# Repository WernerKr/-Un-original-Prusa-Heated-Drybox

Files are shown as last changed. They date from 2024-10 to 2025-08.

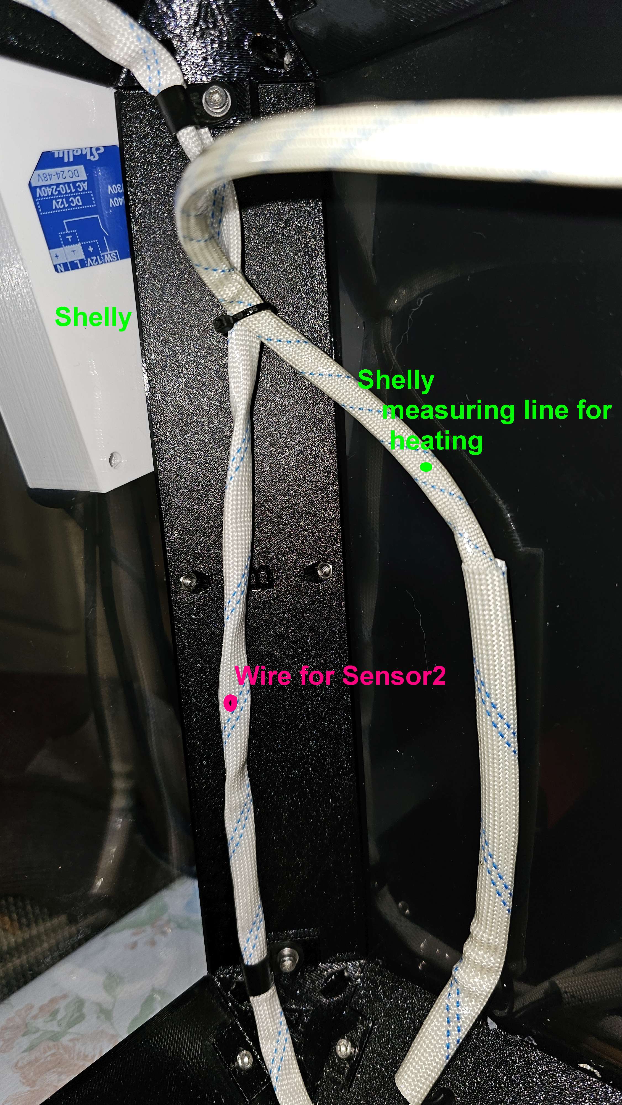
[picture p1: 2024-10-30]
drybox/Wire Sensor2.jpg

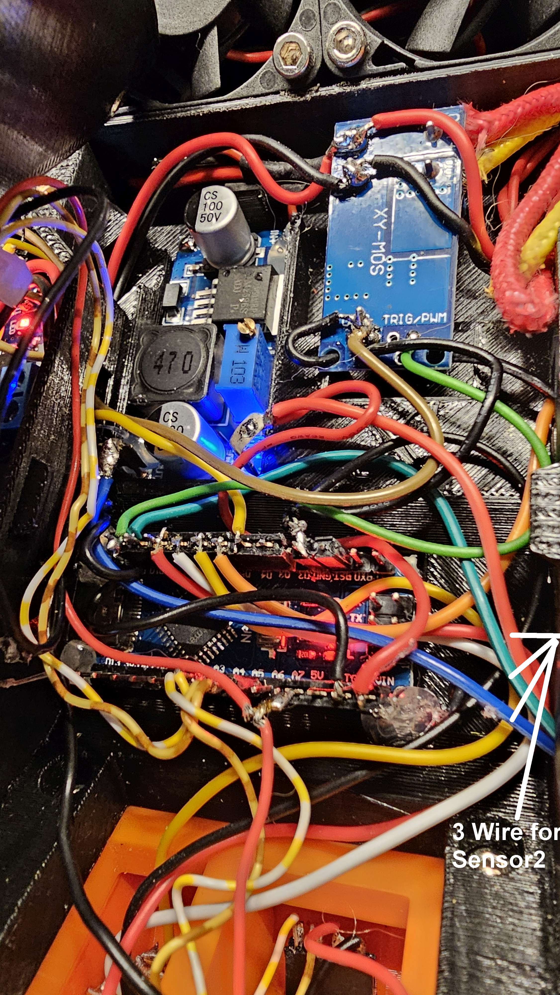
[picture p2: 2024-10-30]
drybox/Wire3 Sensor2.jpg

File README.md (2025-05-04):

## -Un-original-Prusa-Heated-Drybox Code for Ardunio Nano ESP32-S3 Home Assistant

Required processor Arduino Nano ESP32-S3, is pin compatible and has the same dimensions as the Arduino Nano 
with the exception that the 5V pin only supplies a voltage when USB is connected. 
Therefore, no more 5V is taken from this pin, only from buck converter (or Vin Pin, whereas this Pin is always connected to buck converter).
- Invalid values (85°C or -127°C and now too >150°C) are displayed as 0.0 °C/F but are not transmitted to Home Assistant.

#### The esp32 3.1.1 board library is needed!. The newer esp32 3.2.0 board library is causing errors. 

IDE_Arduino_Nano_ESP32
Arduino Nano ESP32 Drybox

### Update 2025-02-07
- Fan run-on now depends on the temperature reached
- If #define BlankScreen and #define BlankScreenAutoOff are active and AutoHum is also active, the screen saver is activated after the heating and fan are off (Pixel).
- To get the display back, press the "Down Button". The display is then activated for 1 minute (countdown 30) and you can then also reduce the target temperature here.
- If the humidity rises again (heating on again), the display is immediately activated again.

##### Graphic AutoHum 27%
AutoHum_27

#### All user settings are now stored in the file arduino_settings.h
- The former "down" Button (was Second Temp/Hum on/off) is now for ScreenSaver
- The former PIN D4 for Led is now D3. 
- The DS18B20 data works only with PIN D4.
- But to use it, the GPIO pin = 7 for D4 must be set.
- To connect the DS18B20 temperature sensors (3 are supported in the program code) a 4.7 KOhm resistor must be used between pin D4 and Vin (=5V). All data lines of the DS18B20 are connected to pin D4 at the same time.
- Since the Arduino Nano Esp32 has a higher internal temperature, the DHT20 heats up more and the temperature value is therefore distorted when the heating is off.
- Therefore, it makes sense to move/mount the DHT20 sensor outside the Z-bracket, perhaps above the Z-bracket near the fan
drybox2_dht20

#### All user settings are now stored in the file arduino_settings.h
- #define debug -> to see the Temp/Hum Data and DS18B20 addresses in the Serial Monitor
- #define showFraction -> all values with decimal values otherwise only integer values
- #define controlLed -> if an LED strip needs to be controlled ("up" Button) in non-heating mode
- #define ControllLedAutooff -> Led on and Temperature >=60°C/140°F (= max. operating temperature LED strip) the led is switched off
- #define SecondTemp -> if a second temp/hum is available - not tested without this - so should now always set
- #define BlankScreen -> on/off ScreenSaver with "down" Button in non-heating mode
- #define UsePixel -> ScreenSaver is "running Pixel" otherwise blank Screen
- #define BlankScreenAutoOff -> if heating is off sreensaver active after 10 minutes - need also #define UsePixel
- #define WATCHDOG -> the program is monitored with WatchDog
- #define HomeAssistant	-> send data to Home Assistant
-         security, lan and Name settings for Home Assistant
- #define DS18B20xx -> also support and show DS18B20 temperature sensors
- #define DS18B20HA -> DS18B20 data also send to Home Assinstant, should only be set after the sensor address assignment has been made
- #define DallasAdrSet -> are the DS18B20 temp sensors adresses above correct? Should be set so that the sensor order always remains the same
- #define DallasSensor1 -> first DS18B20 temp sensors available
- #define DallasSensor2 -> second DS18B20 temp sensors available
- #define DallasSensor3 -> third DS18B20 temp sensors available
- all other settings (targetTemp, targetHum ...)

#### ScreenSaver Mode:
The reason why this function was introduced is that the used OLED display produces "ghost characters" when used for a long time and eventually becomes illegible. This extends its lifespan.
Usage: Switching on/off is only possible in non-heating mode using the "Down" button. As soon as heating mode is started, the ScreenSaver is switched off, with the exception: with AutoHum and the heating and fan are off, the previously set ScreenSaver mode is activated again. There are two types of ScreenSaver: The default is that a pixel moves across the screen every 2 (AutoHum heating mode) or 10 (off mode) seconds. The alternative is (//#define UsePixel - i.e. not active) the screen is completely off.

#### DryBox 
With the appropriate settings, the program behaves just like the DryBox without ESP32, but can easily be expanded with the features of the ESP32 (Wifi, Home Assistant, DS18B20 Temp Sensor).

Home Assistant

### DryBox Home Assitant Graph

drybox_graph
Drybox2_graph

Drybox2_HA
drybox_ds18b20

# -Un-original-Prusa-Heated-Drybox Code for Ardunio (Nano) 
https://www.printables.com/de/model/883817-unoriginal-prusa-heated-drybox

Parts sold from Blurolls: processor ATmega328P (OldBootloader)

DryBox

Heater_off
Heater_on

Heater_offF
TargetTempF

AutoOff
AutoHum

With duct
Drybox_with_duct

## 2024-12-11: Updated files (Serial_20241211.zip)
 - In heating mode, the update and query interval has been reduced to 2 seconds
 - In addition, the temperature control difference was set to 0.1°C / 0.18°F and the humidity control difference (AutoHum) was set to 0.1% humidity.
 - This results in much faster control behavior (Inspired by Sunlu S4)
 - I am now using a modified duct, provided to me by @wbsp. Changes: 
 - the outlet area at the bottom is 5 mm larger and the outlet at the side is 12 mm higher. 
 - This allows for a much greater air flow. 
3D Druck_ 20241213_drybox1
3D Druck_ 20241213_drybox_hum

 ### Comparison with Sunlu S4
 Sunlu_S4_Sensoren2
 3D Druck_ 20241213_Sunlu_S4
 3D Druck_ 20241213_Sunlu_S4_1
 3D Druck_ 20241213_Sunlu_S4_0

## 2024-11-25: Updated files (Serial_20241125.zip)
 With AutoHum, the humidity difference has been reduced to 0.2% (previously 1.0% and 0.5%)
 If the AutoHum function is set below 25%, the TargetTemp is raised to 55°C/131°F, otherwise this humidity is not achieved. 
 The fan run-on time has been slightly reduced at temperatures above 55°C.

Diagram description:
 - At start-up TargetTemp = 50°C, AutoHum = 25%. The front door was still closed. 
 - At around 9:45 the front door was lifted slightly to allow air to circulate. 
 - At 10:30 the AutoHum value was reduced to 20%. Previously, the 25% was reached and regulated
 - After the AutoHum value was not reached at the TargetTemp of 50°C, the TargetTemp was raised to 55°C shortly before 11:00. 
 - With this setting the AutoHum value of 20% was then reached and regulated.
Drybox_Autohum1
Drybox_Autohum2

## 2024-10-15: Updated files (Serial_20241015.zip)
Possibility to switch off the LED strip automatically at 60°C/140°F, 
as the LED strips normally have a maximum operating temperature of 60°C. However, this requires a second Temp/Hum sensor.

## Comparison with/without duct, with/without additional fans
 #### Test environment: 
 - Target temperature 70°C, 
 - AutoOff after 240 minutes (4 hours), 
 - two empty filament rolls in position 2 and position 4.
 - Two front PTFE outlets always open for air exchange. 
 - Overtemperature shutdown of the heater at 90°C, measurement on the floor below the heater/duct
 - Measured with second temp/humidity sensor
 - Graphics from Home Assistant and data from Shelly Plus Add-on and 3 sensors DS18B20 - measuring range -55 °C to +125 °C
   
Drybox

- T1 = Heating temperature
- T2 = Temperature under heating/duct
- T3 = Temperature front right (near door)

### Temperature curve without duct and without additional fans
- The door was lifted slightly after about 1 hour for air exchange and closed again about 5 minutes before the end
- Temperature reached 64.2 °C and 
- temperature under heating 86.9 °C
Drybox_org_vx
### Temperature curve with duct and without additional fan
- The door was raised slightly after 5 minutes and was then raised the whole time for air exchange
- Temperature reached 55.8 °C and 
- temperature under duct 73.0 °C
Drybox_duct_vx
### Temperature curve with duct and with two additional fans below duct
- The door was lifted slightly after 5 minutes and was closed again 5 minutes before the end for air exchange
- Temperature reached 60.2 °C and 
- temperature under duct 71.5 °C
Drybox_fan_vx

## Older test:
#### New: two additional fans below the "duct" for much better air distribution
#### for Bracket Y, Beam A1, Beam A2, Beam A3, Beam A4, duct is now printed with Easy Nylon from Overture.
#### Heat resistance of PC blend is only 113°C/235°F, but over 120°C/248°F is achieved on Bracket Z and duct
#### Easy Nylon has a Heat resistance of 180°C/356°F

Fan 3and4
Fan 3and4_0
Fan 3and4_1
Additonanl_Fan0
Additional_Fan
### New measuring sensors: with Shelly Plus Add-on: DS18B20 - measuring range -55 °C to +125 °C

The second temp/humidity sensor now measures the temperature on the floor under the duct
```
The front door was slightly open
Temperature 2 : Temperature inside duct
Temperature 3 : Temperature Back below duct
Temperature 1 : Temperature front bottom right
Temperature 4 : Temperature rear bottom left
Temperature 5 : Temperature rear bottom right

3D : Temperature/Hum Front bottom right
3DL: Temperature/Hum Back bottom left
3DR: Temperature/Hum Back bottom right
```

### TargetTemp 70°C
TempGraph_TargetTemp70_1
TempGraph_TargetTemp70_2

### TargetTemp 50°C
TempGraph_TargetTemp50


## Heating test series:
```
Sensor Ecowitt WN34AD Temperature range -55..+125°C, Measuring cycle 77 seconds
```
Ecowitt WN34AD_0
```
Sensor DHT21  Temperature range -40..+80°C, here Measuring cycle 5 seonds
```
DHT21
```
Empty Box! With Duct from "morap"
WN34AD in the measuring hole of the duct
Second sensor DHT21 at the bottom of the box under the duct
```
Messung

```
DHT21 Duct: Previous measurement with DHT21 on the duct and temperature limitation at 123°C
```
```
All values are in °C - Time in minutes
Time 	WN34AD	Display	DHT21	DHT21 Duct
5	97.0	34.7	51.2	85
6	100.6	36.3	53.9	90
8	103.4	37.7	56.0	95
9	105.6	39.2	58.0
10	107.4	40.5	59.9
11	108.4	41.7	61.4	100
13	110.2	42.8	62.9	105
14	111.3	43.8	64.2	110
15	112.3	44.8	65.4
17	113.1	45.7	66.2	113	
18	113.8	46.6	67.4	115
19	114.5	47.3	68.2
21	115.1	48.0	69.0
22	115.6	48.7	69.5
23	116.1	49.3	70.2	119
24	116.6	49.9	70.8	
26	116.9	50.4	71.2	121
27	117.3	50.9	71.7	
28	117.6	51.4	72.0	122
29	118.0	51.8	72.4
31	118.2	52.2	72.7	123
32	118.5	52.5	73.0
33	118.8	52.8	73.4
35	119.0	53.1	73.7
36	119.3	53.4	73.9
38	119.6	53.9	74.4
40	120.0	54.2	74.7
41	120.1	54.4	74.9
42	120.2	54.6	75.0
43	120.3	54.8	75.2
45	120.5	55.0	75.4
46	120.7	55.1	75.5
47	120.8	55.3	75.6
49	121.0	55.4	75.8
```
Diagramm
```
3DL shows temperature curve at the rear left.
3D shows temperature curve at the front right
Depends greatly on the temperature at the back in the middle on the floor (directly under the duct last 75.8°C)!

```
### End of testing:
End
Ecowitt WN3434AD_1

## Code files for the heater 

### Main file = Serial.ino
Arduino IDE
ARDUINO_pin_en

Support a second temperature/humidity sensor (DHT21 or DHT22)
You need then additional the Arduino library "DHT-sensor-library"

SecondSensor1
SecondSensor2

Control the fan via a second mosfet
Can Control a led strip via a third mosfet
Heater AutoOff function.
Heater AutoHum function.
Overheating control (with second temperatur/humidity sensor) - not active if no second temp/hum semsor or disabled

Fan control: Vin+ to 24V+, Vin- to 24V-(Gnd), Out+ to Fan red, Out- to Fan black, Gnd to Buck-Convert Out- or Arduino GND
//Arduino pin where the control line for the Mosfet is connected
```
#define Fan 5
```
Led strip control: Vin+ to 24V+, Vin- to 24V-(Gnd), Out+ to Led red, Out- to Led black, Gnd to Buck-Convert Out- or Arduino GND
24V Led strip:
```
#define controlLed
#define Led 4
```
Led_strip_wire
Led_strip1
Led_strip_on

In the program, the second sensor is switched on with
```
#define SecondTemp
or deactivated with //#define SecondTemp
```
The sensor used is specified here
```
#define DHT_TYPE DHT21
//#define DHT_TYPE DHT22
```
The DHT21 is activated here
The data pin of this sensor is set to 9:
```
#define DHT_PIN 9
```
The other pins of this second sensor are to be connected to 5V and GND.

If the second sensor is activated but there is no second sensor,
0.0% and 0.0°C are displayed in the data line.

## Protection for the Wires
High temperature wire protection

If the heating is switched off, you can use the
#### "-" button (= bottom button) to switch on or off to the normal display (no display of the data from the second sensor).
-> Function not available if no second temp/hum sensor present

If the heating is switched off, you can use the
#### "+" button (= middle button) to toggle the LED strip off/on - default is on

In addition, you can use the program to display the data from the temperature/humidity sensors using
```
#define debug (default deactivated with "//#define debug")
```
via the IDE's serial monitor.
But this data are not updated if the AutoOff function is activ!

It is possible to correct the temperature and/or humidity values with a correction value.
```
float TemperatureCor = 0.0;
float HumidityCor = 0.0;
float Temperature2Cor = 0.0;
float Humidity2Cor = 0.0;
//The maximum adjustable temperature is limited to 70°C.
int MaxSet = 70;  
//The overheating temperature is set to 83°C - now measured under the duct!
int Max = 83;   
```
This is because the Arduino should only be operated up to a maximum temperature of 80°C.
If you want a higher temperature, you have to place the electronic components outside the housing! 

When the heating is switched on, you can activate the heating AutoOff mode by pressing the

 ### First and hold the "+" (middle button) and then "on/off" (above button) button.
You may have to try a few times until it works. The display shows then "AutoOff"

AutoOff

The default switch-off value is 360 minutes
```
int AutoOffTime = 360;
```
The maximum time for switching off is 2 days (2880 minutes)
```
int MaxAutoOffTime = 2880; // max 2 days, step 10 minutes
```
The minimum value is 10 minutes.

When the heating is switched on, you can activate the heating AutoHum mode by pressing the
 ### First and hold the "-" (below button) and then "on/off" (above button) button.
You may have to try a few times until it works.  The display shows then "AutoHum"

AutoHum

If the set Humidity value (10-65%), default 35% is reached the heater is switched off
the Fan delay starts and after the set time the fan is also switched off (only with extra Mosfet for fan!)
-> stand by. 
If the Humidity value increase the heater and fan is switched on again
and so on. 

The default Auto Hum value is 25 % - changed from 35% to 25%
```
int TargetHum = 25;
```
The maximum percent for standby = 65 %		// with so high value you can simple test the AutoHum function!
The minimum value is 10%			// This humidity level will probably not be reached with heating!



```
 On the picture you see a AutoHum value of 45% and the Heater is on (ON)
 The humidity value is 44.4% (AutoHum value reached) the Heater is off (on)
 The fan delay starts and the fan is also switched off in 230 seconds (need fan control).
 If the humidity rised to 46% the heater and fan is ON again. 
```
The settings of the AutoOff Minutes and AutoHum times is now automatical done after 30 seconds!
A dot will appear on the far right side if the change of the values of AutoOff or AutoHum is still active.
Otherwise, change the target temperature.

Settings

### Fan Control:
Function: when the heater is switched on, the fan always runs, even if the target temperature has been reached (heating element is switched off).
If the heating element is switched on in normal mode, this is now displayed with "ON".
If switched off, it is displayed with "on".
In AutoOff mode, a switched on heating element is displayed with "A" and a white background, 
if switched off, it is displayed with "A" and a black background.
When overtemperature is reached, "Hi" is displayed instead of "ON" and the heater is switched off until the temperature drops again.
In AutoOff mode instead of "A" then "H"

 Vertical Display hiTemp

When the heater is switched off (directly or via AutoOff), the fan continues to run for an adjustable time:
```
int FanDelay = 300;
```
Vertical Display

This run-on time is then counted down in the display after switching off.
The fan shutdown time now depends on the selected target temperature (60 - 900 seconds)

If you have installed a second temperature sensor, you can with 
```
bool overHeat = true;
```
monitor the temperature directly on the heating element and when the max temperature (°C)
```
int Max = 83;		// = 181 °F
```
is reached, the heating is also switched off (fan continues to run if second Mosfet is used)

Other settings:
```
#define showFraction
```
Now also in the State Line the Temperatur or Humidity are shown with fraction.
If you like the former showing (only Integer) uncomment //#define showFraction

AutoOff_HeaterOn_secondSensor_showFraction
AutoOff_HeaterOn_secondSensor_not_showFraction

If Duct is installed, the system is slower, so the change temperature is set to 0.2°C here, otherwise 0.5°C
```
bool withDuct = true;                     // Duct installed -> Tempdiff = 0.2°C otherwise 0.5°C
```

### But be careful: 
    all electronic components used (temp sensor, Arduino, etc.) are only designed for a maximum ambient temperature of 80°C (176°F).
    And you should also note: Maximum operating temperature of the fan is 70°C
    If using inside the (Un)original Prusa Heated Drybox a LED strip you should know:
    the maximum operating temperature of the LED strip is normally 60°C! 

#### Warning!
     If the fan control is not used, the fans must be permanently connected to the 24 V voltage.
     The display behaves as if the additional fan control were present, showing a countdown in seconds for the fan to shut down!

#### My recommendation for the filament to be used for "Bracket Y" and "condotto 5" is Nylon 
#### or an even higher temperature resistant filament.
#### In my experience, even PC blend or ASA is not suitable!

### Also important!
    When the heating is on, air exchange must be able to take place, 
    e.g. by lifting the front door or using the unused PTFE outlets, 
    otherwise humidity reduction cannot take place.



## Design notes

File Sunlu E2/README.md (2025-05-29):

## Sensors used:
- Sonoff SNZB-02D (Temperatures from -9.9°C to +60°C ) stopped at 59.9 °C - removed for Target 90°C and 110°C
- DHT20: Sunlu Temperatur außen unten (Temperatures from -40°C to +80°C ) but masures above +80°C
- DHT22: Sunlu Temperatur Innen (Temperatures from -40°C to +80°C ) but measures above +80°C 
- DS18B20: Sunlu Temp1, Temp2, Temp3 (Measures Temperatures from -55°C to +125°C ) stopped at 127.94 °C
- Camera: Flir One Pro
- Recording via Arduino Nano ESP32-S3
- Evaluation via Home Assistant
E2_Sensorsx_txt
Sunlu_E2_00

## Diagram at Target temperature 70°C, 90°C and 110°C
### Settings: Target temperature 70°C
#### Temperature and consumption diagram of the Sunlu E2 dryer 70°C
E2_70x

Sunlu_E2_70x
Sunlu_E2_70_1x
Sunlu_E2_70_2x
##### Inside
E2_inside_70x
##### Temperatures after switching off (70°C)
E2_after_Switch_offx
##### after 3 minutes (70°C)
E2_and_then_after_Switch_off_3minx

### Settings: Target temperature 90°C
#### Temperature and consumption diagram of the Sunlu E2 dryer 90°C
Sunlu_E2_90x
Sunlu_E2_90_1x
Sunlu_E2_90_2x

### Settings: Target temperature 110°C (max reached 106.13°C sucking the air) 
E2_Set_110x
#### Temperature and consumption diagram of the Sunlu E2 dryer 110°C
Sunlu_E2_110x
Sunlu_E2_110_1x
Sunlu_E2_110_2x
Sunlu_E2_110_3x
Sunlu_e2_110_end

### Inside
E2_Heating_110x
E2_Heating_110_2

### Outside (110°C)
E2_outside_frontx
E2_outside_front2x
E2_Outside_2x

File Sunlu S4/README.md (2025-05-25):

# Settings: Target temperature 70°C
#### Sensors used:
 - Sonoff SNZB-02D
 - DHT20: Sunlu Temperatur außen unten
 - DHT22: Sunlu Temp vor Ansaug
 - DS18B20: Sunlu Temp1, Temp2, Temp3
 - Camera: Flir One Pro
 - Recording via Arduino Nano ESP32-S3
 - Evaluation via Home Assistant

## Temperature and consumption diagram of the Sunlu S4 dryer
Sunlu S4

Sunlu_S4_00
Sunlu_S4_0
Sunlu_S4_1
Sunlu_S4_2

## Power consuption diagrams
Sunlu_S4_Leistung
Sunlu_S4_Leistung1
Sunlu_S4_Leistung2

## Temperature inside the dryer
2025-05-22 10 50 39x
2025-05-22 10 50 48x
2025-05-22 10 54 17x
2025-05-22 10 54 58x

## Outside Front
2025-05-22 10 53 21x
2025-05-22 10 49 52x
2025-05-22 10 51 31x
2025-05-22 10 42 24x

## older diagrams
3D Druck_ 20241213_Sunlu_S4_0
3D Druck_ 20241213_Sunlu_S4_1
3D Druck_ 20241213_Sunlu_S4

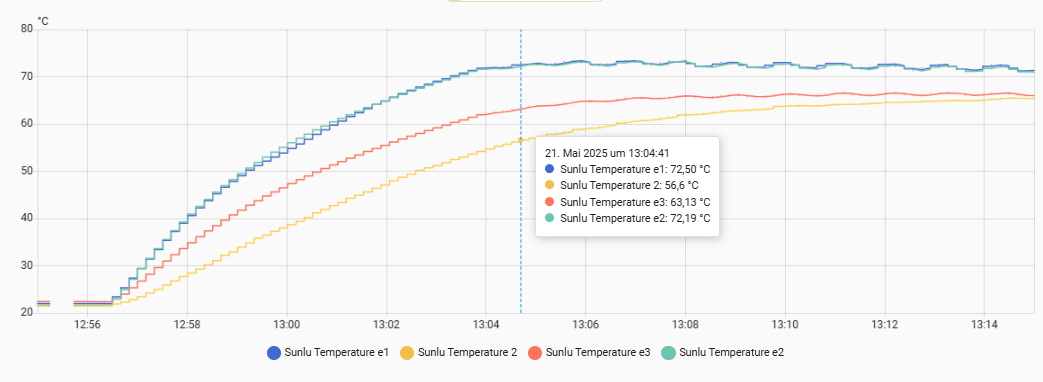
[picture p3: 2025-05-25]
Sunlu S4/Sunlu_S4_00.png

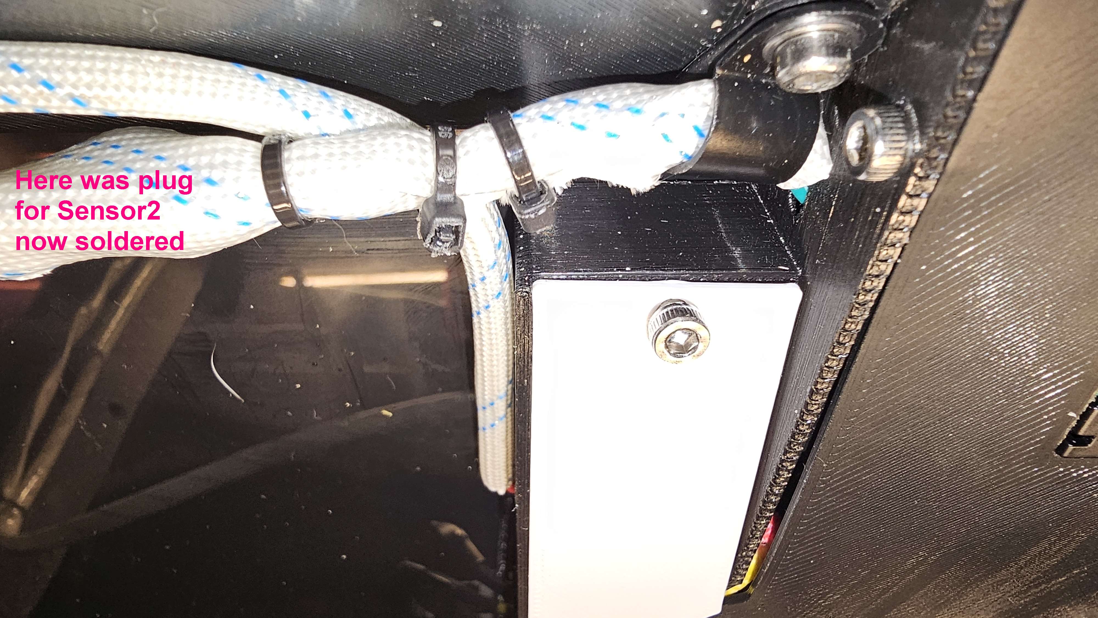
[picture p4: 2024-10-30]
drybox/Wire2 Sensor2.jpg

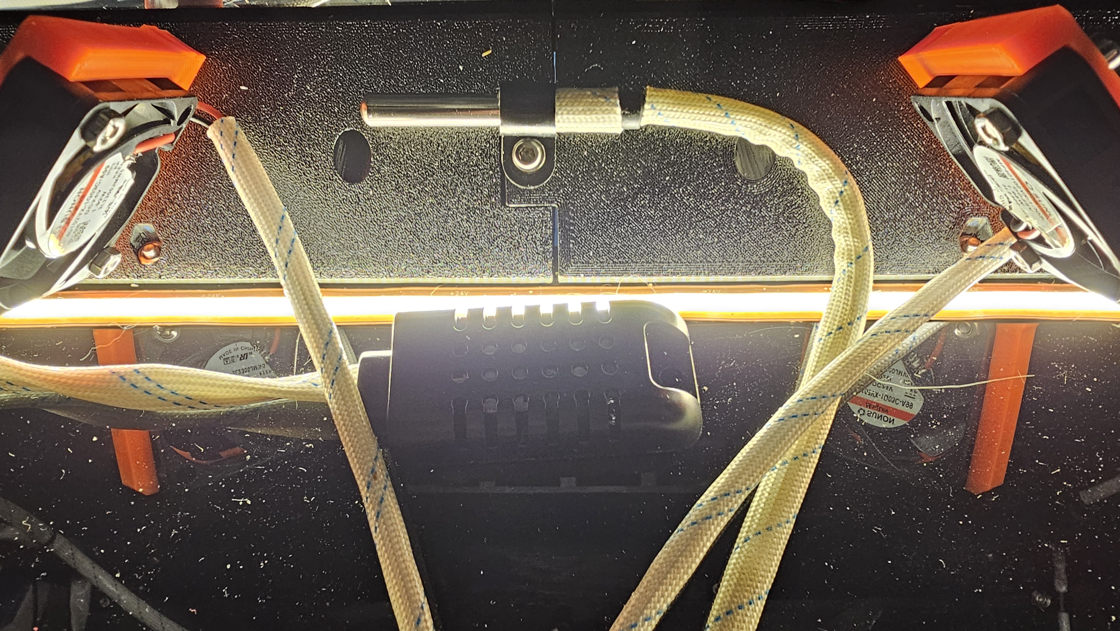
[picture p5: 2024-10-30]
drybox/Sensor2 lying on the floor behind and in front of the LED strip.jpg

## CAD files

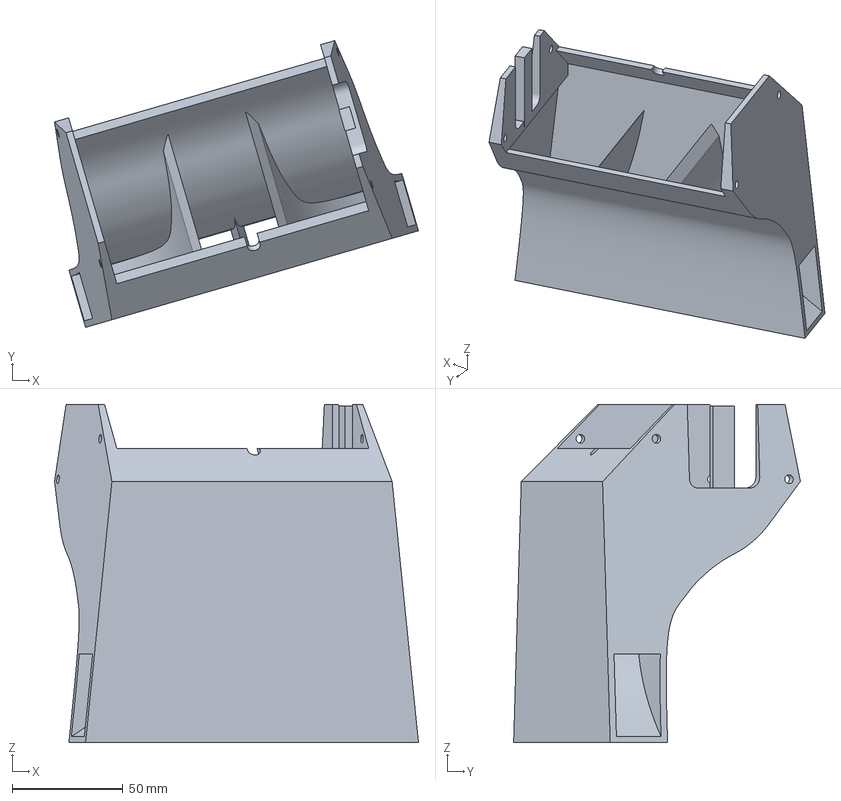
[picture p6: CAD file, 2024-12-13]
drybox/condotto 6 quer Nylon_re.3mf
164.4 x 129.6 x 152.8 mm

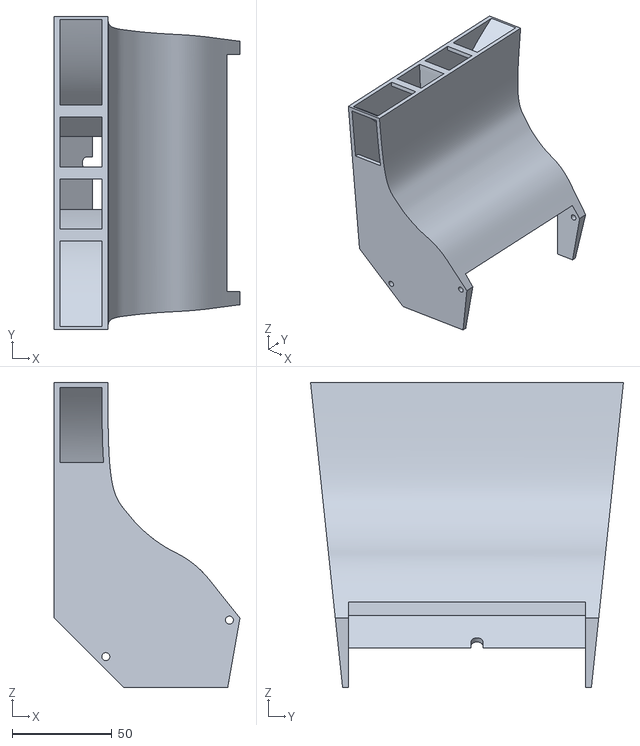
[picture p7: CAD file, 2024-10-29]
drybox/werner-duct-augment.stl
93.0 x 156.6 x 152.8

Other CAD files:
drybox/condotto 6 quer Nylon_y6_re.3mf

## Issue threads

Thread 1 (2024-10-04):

Modification ideas: ESP8266; encoder; DS18B20 temperature sensors

maximweb, 2024-10-04:
Hi there,

I am currently in the process of upgrading my MK4(soon to be S) with MMU3 and the (un)original heated drybox. When scouting for possible modifications, I saw your very interesting mod.

I have some ideas for further modifications, which I hope are worth sharing.

**Switch from Arduino to ESP8266**

Your images indicate that you are using Shelly products to log the temperatures, and it somewhat looked like Home Assistant. Hence, I was thinking about replacing the Arduino with a wifi-capable ESP8266/NodeMCU. This could then push all the sensor data to a self-hosted MQTT server enabling logging and live review of the heater's performance without the need of additional Shelly hardware. (I've some working not-yet-published code for ESP8266 and MQTT, which I could contribute.)

**Replace some buttons with a rotary encoder**

Another tweak I can think of, vastly improving flexibility, is to replace some of the buttons with a rotary encoder. This gives significant more flexibility and allows to built an entire menu structure. In addition to setting the target temperature, this would also allow to adjust [multiple settings, currently hardcoded](https://github.com/WernerKr/-Un-original-Prusa-Heated-Drybox/blob/main/Serial.ino#L63-L70).

I would love to get your take on my suggestions. It might take some weeks until I have all the default parts for the enclosure ready, but I am willing to contribute some code, as I have helpful bits and pieces already lying around on my harddrive somewhere.

WernerKr, 2024-10-04:
>I was thinking about replacing the Arduino with a wifi-capable ESP8266/NodeMCU
I had this idea too and have even bought an Arduino Nano ESP32 with Headers [ABX00083] – ESP32-S3, USB-C, WLAN, Bluetooth, HID support, MicroPython compatible
But I haven't done anything with it yet.

>Shelly products to log the temperatures, and it somewhat looked like Home Assistant.
Yes. The Selly plus 1 with Add-on plus is a device in Home Assistant und here I can log the temperatures of (un)original heated drybox.
Why Selly?
Is an independent device outside the dry box, **i.e. not exposed to high temperatures**,
the DS18B20 sensor can measure temperatures of up to 125°C and can switch off the voltage
from the heating element in the event of overheating without an additional device.
It is important that the fans continue to run.
The Shelly is only intended for additional security.
Is currently available for recording temperatures, as I have not found any other way to record such high temperatures and transmit them for evaluation

I have tried to use the DS18B20 sensors directly now as well.
They are not recognized, but they work because they are recognized by the Shelly.
I haven't yet found out the reason for this.

>Replace some buttons with a rotary encoder
I think this is a prerequisite for further expansion.

I think your suggestions are excellent

maximweb, 2024-10-04:
> > I was thinking about replacing the Arduino with a wifi-capable ESP8266/NodeMCU
>
> I had this idea too and have even bought an Arduino Nano ESP32 with Headers [ABX00083] – ESP32-S3, USB-C, WLAN, Bluetooth, HID support, MicroPython compatible But I haven't done anything with it yet.

I just looked it up, didn't realize that there is an Arduino ESP. Must have missed that, thanks. I have a bunch of different versions of ESP8266 board, though. My last attempt to MicroPython was some years ago, and I had trouble getting it work reliably. But I never revisited it since. For such possibly dangerous applications, I would always opt for Arduino (C/C++) code.

> > Shelly products to log the temperatures, and it somewhat looked like Home Assistant.
>
> Yes. The Selly plus 1 with Add-on plus is a device in Home Assistant und here I can log the temperatures of (un)original heated drybox. Why Selly? Is an independent device outside the dry box, **i.e. not exposed to high temperatures**, the DS18B20 sensor can measure temperatures of up to 125°C and can switch off the voltage from the heating element in the event of overheating without an additional device. It is important that the fans continue to run. The Shelly is only intended for additional security. Is currently available for recording temperatures, as I have not found any other way to record such high temperatures and transmit them for evaluation

Thank you for the info, I had not really thought about the electronics overheating. Maybe I opt for moving all electronics to the outside of the box. Maybe next to the PSU.

> I have tried to use the DS18B20 sensors directly now as well. They are not recognized, but they work because they are recognized by the Shelly. I haven't yet found out the reason for this.

DS18B20 can be tricky. They easily damage when connecting them in the wrong way. In addition, they are very picky regarding the value of the pullup resistor on the data line. [Some reference code from one of my projects.](https://github.com/brewpeople/brewslave/tree/master/libs/ds18b20)

maximweb, 2024-10-08:
I hope it's ok that I hijack this issue to report my latest findings and progress.

I've read your notes regarding the temperature distribution being poor without additional external fans.

Hence, I had a look at the [duct](https://www.printables.com/model/951757-duct-for-unoriginal-prusa-heated-drybox) I believe you are using.

**I think the design of the duct has two flaws, which when fixed, might make the additional fans unnecessary.** The original design divides the entire cross section in three even sections. The outer ones direct the hot air sideways and the central one downwards. The flaw I see in this is that the cross section of the duct includes the black plastic frame of the heater, while the air from the fans solely flows through the metal parts.

This results in most of the hot air flowing in the central section and hence downward, whereas only a small portion of air is taking the outer section directed towards the sides.

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

Therefore, I am in the process of **redesigning the duct** with the following changes:
* significantly decrease the width of the central section, directing more air towards the sides
* widening the entire base of the duct, placing the side outlets further apart.

Here a sneak peek:

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

So far, I have only printed in PETG as design test. Running the fans without heating, I can confirm that most of the air is exiting the duct sideways. As of yet, I never printed with Nylon and still waiting for my order to arrive. I hope i get this printed without warping.

PS: I also ordered an Arduino Nano ESP32. Some more printing of basic frame parts to do, before I can start coding.

WernerKr, 2024-10-08:
Hi,

> might make the additional fans unnecessary
I think that the two additional fans have a positive effect on the air
distribution, especially towards the front

In my opinion, the upper distribution is OK, It divides the heating area
into 3 equal parts.
The problem is the side outlet, which is much smaller than the one assigned
above.

I therefore also increased the side outlets by 15mm.
I have to say that I haven't been doing 3D printing for very long and don't
have enough experience.
I can only make changes with the PrusaSlicer using Add Part or Add negative
volume.
> widening the entire base of the duct, placing the side outlets further
apart.
I also suggested this to the "duct" creator, but he never responded
> I hope i get this printed without warping.
With Easy Nylon form Overture (printed with 260°C) no Problem with Warping
But on Strong overhangs create blobs.
No need of Supports. I also tried using supports, but the blobs were even
worse.

See attached pictures.

Werner

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
WernerKr, 2025-01-02:
> Sorry to highjack your project.

No Problem!

I tried to query DS18B20 temperature sensors with the "normal" Nano, but was unsuccessful.
After that, I didn't have time to worry about why.

I have already seen MQTT with Home Assistant:
For example, use HomeAssistantEntities and MQTTRemote

Why "moved to VSCode and PlatformIO for development" ?

> and publish it even before its finished

I would be very interested in that

maximweb, 2025-01-02:
> > Sorry to highjack your project.
>
> No Problem!

I appreciate it 🥇

> I tried to query DS18B20 temperature sensors with the "normal" Nano, but was unsuccessful. After that, I didn't have time to worry about why.

I've used them before, but struggle time and time again.

> I have already seen MQTT with Home Assistant: For example, use HomeAssistantEntities and MQTTRemote

Did this before with an ESP8266. So I hope this will be an easy task.

> Why "moved to VSCode and PlatformIO for development" ?

I don't like the Arduino IDE and I am used to VSCode. It is my first attempt with PlatformIO and it seems to work quite trouble-free.

> > and publish it even before its finished
>
> I would be very interested in that

I've published my current state, but it is far from complete: https://github.com/maximweb/drybox-esp32

At the moment I am still working on various individual parts. Still some way to go before putting everything together.

WernerKr, 2025-01-06:
My Testversion for Home Assistant and MQTT support is now ready - are Arduino IDE files!
see drybox_Home_Assistant_MQTT  - Hardware Arduino Nano ESP32-S3

WernerKr, 2025-01-07:
> The additional temperature sensors gave me trouble so I pushed it aside for a while. But two days ago I finally fixed this.
What was/is the solution to the problems with the DS18B20 sensors?

--------------------------------------------
Werner Krenn
Lackenhäuser 149
D-94089 Neureichenau
Germany

***@***.*** ***@***.***>
***@***.*** ***@***.***>

https://www.pc-wetterstation.de
--------------------------------------------

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

maximweb, 2025-01-07:
> What was/is the solution to the problems with the DS18B20 sensors?

The standard things:
* I use the [DallasTemperature](https://github.com/milesburton/Arduino-Temperature-Control-Library) library
* The data line needs a 4.7kOhm pullup resistor (for long cables in the tenth or hundred meter, use less)
* DS18B20 is allergic (damages easily) when GND and VCC pins are swapped, so take extra care to check

Nano ESP32 specific
* There is something called pin-remap for the Nano ESP32. It seems [the OneWire library required for DallasTemperature does not (yet)support this](https://github.com/PaulStoffregen/OneWire/issues/148). This meant i had to use the GPIO pin number for it to work.
  * I am still not entirely sure how the remapping works, but OneWire always needs a [GPIO pin number](https://docs.arduino.cc/tutorials/nano-esp32/cheat-sheet/#esp32-pin-map).
  * This can lead to conflicts as when pin remapping is disabled: Never use `Dx` names for pins and pure numbers combined.
* I had to set `pinMode(<your pin>, OUTPUT)` explicitly for the data pin, despite it being used as combined input and output. This is probably related to the remapping issue.

WernerKr, 2025-01-08:
Thank you very much.

I have now completed a version for Home Assistant support with
Arduino Nano ESP32-S3 for the (un)original heated Drybox (IDE files). See  <https://github.com/WernerKr/-Un-original-Prusa-Heated-Drybox> https://github.com/WernerKr/-Un-original-Prusa-Heated-Drybox and there "drybox_Home Assistant_MQTT"

Werner

--------------------------------------------
Werner Krenn
Lackenhäuser 149
D-94089 Neureichenau
Germany

***@***.*** ***@***.***>
***@***.*** ***@***.***>

https://www.pc-wetterstation.de
--------------------------------------------

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

WernerKr, 2025-01-24:
Since the switch to the Arduino Nano ESP32 is now complete and the data also arrives at Home Assistant both without additional DS18B20 and with this temperature sensor, I now close here

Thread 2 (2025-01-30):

Compilation error: 'HAname' was not declared in this scope; did you mean 'rename'?`

ttrueten, 2025-01-30:
Hi,
The compilation of the [drybox_Home Assistant_MQTT](https://github.com/WernerKr/-Un-original-Prusa-Heated-Drybox/tree/main/drybox_Home%20Assistant_MQTT) code aborts with the following message:

`/home/tht/Arduino/drybox2_Home Assistant_MQTT/Drybox2/Drybox2.ino: In function 'void setupJsonForThisDevice()':
/home/tht/Arduino/drybox2_Home Assistant_MQTT/Drybox2/Drybox2.ino:206:35: error: 'HAname' was not declared in this scope; did you mean 'rename'?
  206 |   _json_this_device_doc["name"] = HAname;
      |                                   ^~~~~~
      |                                   rename
/home/tht/Arduino/drybox2_Home Assistant_MQTT/Drybox2/Drybox2.ino: At global scope:
/home/tht/Arduino/drybox2_Home Assistant_MQTT/Drybox2/Drybox2.ino:216:34: error: 'HAnamelower' was not declared in this scope
  216 | HaBridge ha_bridge(_mqtt_remote, HAnamelower, _json_this_device_doc);
      |                                  ^~~~~~~~~~~
/home/tht/Arduino/drybox2_Home Assistant_MQTT/Drybox2/Drybox2.ino:229:62: error: 'HAtemptarg' was not declared in this scope
  229 | HaEntityTemperature _ha_entity_temperature_target(ha_bridge, HAtemptarg, HAtemptargtxt);
      |                                                              ^~~~~~~~~~
/home/tht/Arduino/drybox2_Home Assistant_MQTT/Drybox2/Drybox2.ino:229:74: error: 'HAtemptargtxt' was not declared in this scope
  229 | HaEntityTemperature _ha_entity_temperature_target(ha_bridge, HAtemptarg, HAtemptargtxt);
      |                                                                          ^~~~~~~~~~~~~
/home/tht/Arduino/drybox2_Home Assistant_MQTT/Drybox2/Drybox2.ino:230:55: error: 'HAtemp' was not declared in this scope; did you mean 'mktemp'?
  230 | HaEntityTemperature _ha_entity_temperature(ha_bridge, HAtemp, HAtemptxt);
      |                                                       ^~~~~~
      |                                                       mktemp
/home/tht/Arduino/drybox2_Home Assistant_MQTT/Drybox2/Drybox2.ino:230:63: error: 'HAtemptxt' was not declared in this scope
  230 | HaEntityTemperature _ha_entity_temperature(ha_bridge, HAtemp, HAtemptxt);
      |                                                               ^~~~~~~~~
/home/tht/Arduino/drybox2_Home Assistant_MQTT/Drybox2/Drybox2.ino:231:57: error: 'HAtemp2' was not declared in this scope
  231 | HaEntityTemperature _ha_entity_temperature_2(ha_bridge, HAtemp2, HAtemp2txt);
      |                                                         ^~~~~~~
/home/tht/Arduino/drybox2_Home Assistant_MQTT/Drybox2/Drybox2.ino:231:66: error: 'HAtemp2txt' was not declared in this scope
  231 | HaEntityTemperature _ha_entity_temperature_2(ha_bridge, HAtemp2, HAtemp2txt);
      |                                                                  ^~~~~~~~~~
/home/tht/Arduino/drybox2_Home Assistant_MQTT/Drybox2/Drybox2.ino:278:56: error: 'HAhumtarg' was not declared in this scope
  278 | HaEntityHumidity _ha_entity_humidity_target(ha_bridge, HAhumtarg, HAhumtargtxt);
      |                                                        ^~~~~~~~~
/home/tht/Arduino/drybox2_Home Assistant_MQTT/Drybox2/Drybox2.ino:278:67: error: 'HAhumtargtxt' was not declared in this scope
  278 | HaEntityHumidity _ha_entity_humidity_target(ha_bridge, HAhumtarg, HAhumtargtxt);
      |                                                                   ^~~~~~~~~~~~
/home/tht/Arduino/drybox2_Home Assistant_MQTT/Drybox2/Drybox2.ino:279:49: error: 'HAhum' was not declared in this scope
  279 | HaEntityHumidity _ha_entity_humidity(ha_bridge, HAhum, HAhumtxt);
      |                                                 ^~~~~
/home/tht/Arduino/drybox2_Home Assistant_MQTT/Drybox2/Drybox2.ino:279:56: error: 'HAhumtxt' was not declared in this scope
  279 | HaEntityHumidity _ha_entity_humidity(ha_bridge, HAhum, HAhumtxt);
      |                                                        ^~~~~~~~
/home/tht/Arduino/drybox2_Home Assistant_MQTT/Drybox2/Drybox2.ino:280:51: error: 'HAhum2' was not declared in this scope
  280 | HaEntityHumidity _ha_entity_humidity_2(ha_bridge, HAhum2, HAhum2txt);
      |                                                   ^~~~~~
/home/tht/Arduino/drybox2_Home Assistant_MQTT/Drybox2/Drybox2.ino:280:59: error: 'HAhum2txt' was not declared in this scope
  280 | HaEntityHumidity _ha_entity_humidity_2(ha_bridge, HAhum2, HAhum2txt);
      |                                                           ^~~~~~~~~

exit status 1

Compilation error: 'HAname' was not declared in this scope; did you mean 'rename'?/home/tht/Arduino/drybox2_Home Assistant_MQTT/Drybox2/Drybox2.ino: In function 'void setupJsonForThisDevice()':
/home/tht/Arduino/drybox2_Home Assistant_MQTT/Drybox2/Drybox2.ino:206:35: error: 'HAname' was not declared in this scope; did you mean 'rename'?
  206 |   _json_this_device_doc["name"] = HAname;
      |                                   ^~~~~~
      |                                   rename
/home/tht/Arduino/drybox2_Home Assistant_MQTT/Drybox2/Drybox2.ino: At global scope:
/home/tht/Arduino/drybox2_Home Assistant_MQTT/Drybox2/Drybox2.ino:216:34: error: 'HAnamelower' was not declared in this scope
  216 | HaBridge ha_bridge(_mqtt_remote, HAnamelower, _json_this_device_doc);
      |                                  ^~~~~~~~~~~
/home/tht/Arduino/drybox2_Home Assistant_MQTT/Drybox2/Drybox2.ino:229:62: error: 'HAtemptarg' was not declared in this scope
  229 | HaEntityTemperature _ha_entity_temperature_target(ha_bridge, HAtemptarg, HAtemptargtxt);
      |                                                              ^~~~~~~~~~
/home/tht/Arduino/drybox2_Home Assistant_MQTT/Drybox2/Drybox2.ino:229:74: error: 'HAtemptargtxt' was not declared in this scope
  229 | HaEntityTemperature _ha_entity_temperature_target(ha_bridge, HAtemptarg, HAtemptargtxt);
      |                                                                          ^~~~~~~~~~~~~
/home/tht/Arduino/drybox2_Home Assistant_MQTT/Drybox2/Drybox2.ino:230:55: error: 'HAtemp' was not declared in this scope; did you mean 'mktemp'?
  230 | HaEntityTemperature _ha_entity_temperature(ha_bridge, HAtemp, HAtemptxt);
      |                                                       ^~~~~~
      |                                                       mktemp
/home/tht/Arduino/drybox2_Home Assistant_MQTT/Drybox2/Drybox2.ino:230:63: error: 'HAtemptxt' was not declared in this scope
  230 | HaEntityTemperature _ha_entity_temperature(ha_bridge, HAtemp, HAtemptxt);
      |                                                               ^~~~~~~~~
/home/tht/Arduino/drybox2_Home Assistant_MQTT/Drybox2/Drybox2.ino:231:57: error: 'HAtemp2' was not declared in this scope
  231 | HaEntityTemperature _ha_entity_temperature_2(ha_bridge, HAtemp2, HAtemp2txt);
      |                                                         ^~~~~~~
/home/tht/Arduino/drybox2_Home Assistant_MQTT/Drybox2/Drybox2.ino:231:66: error: 'HAtemp2txt' was not declared in this scope
  231 | HaEntityTemperature _ha_entity_temperature_2(ha_bridge, HAtemp2, HAtemp2txt);
      |                                                                  ^~~~~~~~~~
/home/tht/Arduino/drybox2_Home Assistant_MQTT/Drybox2/Drybox2.ino:278:56: error: 'HAhumtarg' was not declared in this scope
  278 | HaEntityHumidity _ha_entity_humidity_target(ha_bridge, HAhumtarg, HAhumtargtxt);
      |                                                        ^~~~~~~~~
/home/tht/Arduino/drybox2_Home Assistant_MQTT/Drybox2/Drybox2.ino:278:67: error: 'HAhumtargtxt' was not declared in this scope
  278 | HaEntityHumidity _ha_entity_humidity_target(ha_bridge, HAhumtarg, HAhumtargtxt);
      |                                                                   ^~~~~~~~~~~~
/home/tht/Arduino/drybox2_Home Assistant_MQTT/Drybox2/Drybox2.ino:279:49: error: 'HAhum' was not declared in this scope
  279 | HaEntityHumidity _ha_entity_humidity(ha_bridge, HAhum, HAhumtxt);
      |                                                 ^~~~~
/home/tht/Arduino/drybox2_Home Assistant_MQTT/Drybox2/Drybox2.ino:279:56: error: 'HAhumtxt' was not declared in this scope
  279 | HaEntityHumidity _ha_entity_humidity(ha_bridge, HAhum, HAhumtxt);
      |                                                        ^~~~~~~~
/home/tht/Arduino/drybox2_Home Assistant_MQTT/Drybox2/Drybox2.ino:280:51: error: 'HAhum2' was not declared in this scope
  280 | HaEntityHumidity _ha_entity_humidity_2(ha_bridge, HAhum2, HAhum2txt);
      |                                                   ^~~~~~
/home/tht/Arduino/drybox2_Home Assistant_MQTT/Drybox2/Drybox2.ino:280:59: error: 'HAhum2txt' was not declared in this scope
  280 | HaEntityHumidity _ha_entity_humidity_2(ha_bridge, HAhum2, HAhum2txt);
      |                                                           ^~~~~~~~~

exit status 1

Compilation error: 'HAname' was not declared in this scope; did you mean 'rename'?`

Any hints? What did I do wrong?

Greetings,
Thomas aka [spambouncer](https://www.printables.com/@SpamBouncer_90037)

ttrueten, 2025-01-30:
Ah, new code. I pulled the version you uploaded an hour ago again. It seems that a few variables were not set appropriately. Compiling now works, thanks for the hint and the update, you can close the issue.
Regards,
Thomas

Closed 2025-01-30.

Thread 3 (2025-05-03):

Unable to compile code for Un-original-Prusa-Heated-Drybox Code for Ardunio Nano ESP32-S3 Home Assistant.

llabarrec, 2025-05-03:
Would you please specify the apps, e.g. arduino ide, platformio used to compile your code, and their parameters?

I have printed the parts and installed the electronics for the project.

I have tried unsuccessfully to compile the code for the arduino nano esp32 board using arduino ide, platformIO, arduino CLI in both Windows 11 and Linux Ubuntu.

I got errors requiring C++17 and multiple others, most of which I overcame using ChatGPT.  I can’t figure out what I am doing wrong.

As a last resort, I am asking you for the environment you used to compile your code.

Thanks

WernerKr, 2025-05-04:
I'm using Arduino IDE 2.3.6 under Windows 10 and, crucially, the esp32_3.11 board library. The newer esp32_3.2.0 board library is causing the errors you mentioned. I haven't investigated why this is happening. The other libraries I'm using (ArduinoJson, MQTTRemote, HaBridge, DallasTemperature, etc.) are all the latest versions.

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

jshank, 2025-08-15:
Board library esp32 by Espressif Systems **version 3.1.1** was the trick for me to get out of C++ 17 errors.

Select `Arduino Nano ESP32 - esp32` NOT the build in `Arduino Nano` in Arduino IDE 2.3.6.

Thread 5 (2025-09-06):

ESP32 libraries

wigw, 2025-09-06:
hi friend. your development, this is what I was looking for for a long time.
thank you for this masterpiece.
I have a problem. arduino nano esp32, what libraries are needed? I want to ask for a complete list of libraries, preferably with links

WernerKr, 2025-09-14:
If you haven't set the option
//#define DallasAdrSet
in arduino_settings_.h,
i.e., you've removed "//".
All addresses are allowed.
The addresses are displayed if
#define debug
is set (is the default in arduino_settings_.h)
and Serial Monitor is enabled.

The connection pin for the DS18B20 (not SD18B20 ?! ) is important.
#define ONE_WIRE_BUS 7 //D4 - GPIO7,
and To connect the DS18B20 temperature sensors (3 are supported in the program code) a 4.7 KOhm resistor must be used between pin D4 and Vin (=5V).

wigw, 2025-09-14:
thank you very much. ds18b20 started measuring temperature. very important question, the most important thing. I have a home assistant server + mqtt broker, how do I connect esp32? from this [link](https://newbiely.com/tutorials/arduino-nano-esp32/arduino-nano-esp32-mqtt) I saw the esp32 ip, according to your code esp32 does not connect to wifi. maybe I installed the wrong libraries?

wigw, 2025-09-14:
I tried to uncomment #define HomeAssistant. arduino ide asks for two libraries, HaBridge.h and Json.h. I couldn't find these two libraries anywhere. Can I get a link?

#define MQTT_HOST "192.???.???.???" is the ip of home assistant?

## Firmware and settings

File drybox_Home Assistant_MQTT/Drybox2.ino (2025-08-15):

/* 
Code for the (Un)original Prusa Drybox Heater
Written by Bram Elema, Creative Commons BY-NC-SA

Added support for a second temp/hum Sensor DHT21 or DHT22
and AutoOff Function 
and AutoHum Function
and new Fan control, and Led Strip control
and DS18B20 Temperatur sensors - 3 pieces are planned in the program
and transfer to Home Assistant
and ScreenSaver
and now Fan run-on now depends on the temperature reached

If heater is set on, the data now updated each 2 sec otherwise 10 sec 
The TargetTemp is now 50°C, the AutoHum ist now 25%
Update Display if Heating on is now 2 sec, 
Should not be less than 2 seconds, due to query temperature sensors
tempDiff is now 0.1°C/0.18°F
humDif is 0.2%
This settings can be canged in arduino_settings.h

Caution! Led Pin is now 3 (was former 4) 
         because DS18B20 works for me only on PIN 4 = GPIO7 !!
Werner Krenn - last modified 
*/
char swversion[12] = "2025-08-15";
/*
REQUIRES the following Arduino libraries:
 - Adafruit_GFX Library: https://github.com/adafruit/Adafruit-GFX-Library
 - Adafruit_SSD1306 Library: https://github.com/adafruit/Adafruit_SSD1306
 - DFRobot_DHT20 Sensor Library: https://github.com/DFRobot/DFRobot_DHT20
 - DHT_sensor_library Library: https://github.com/adafruit/DHT-sensor-library
 - OneWire
 Arduino Nano ESP32:
 - Arduino ESP32
 - ESP32 core v3.x.x
 HA MQTT:
 - ArduinoJson https://arduinojson.org/?utm_source=meta&utm_medium=library.properties
 - MQTTRemote
 - MQTT 
 - HomeAssistantEntities https://github.com/Johboh/HomeAssistantEntities
 DS18B20 Temperature Sensor:
 - DallasTemperature
*/

#include <Arduino.h>
// This is for the Arduino IDE, where we always build with ArduinoJson. arduino-cli will not build/include libraries
// that are not included anywhere. So we must include ArduinoJson.h so its available for IJson.h later.

#include "arduino_settings.h"

#include <esp_task_wdt.h>
#define WDT_TIMEOUT 20 
esp_err_t ESP32_ERROR;

#ifndef PLATFORMIO
#include <ArduinoJson.h>
#endif

#ifdef HomeAssistant
 #include <HaBridge.h>
 // This is here for CI only. You can remove this include and include ArduinoJson.h or nlohmann/json.hpp directly.
 #include <IJson.h>
 #include <MQTTRemote.h>

 #include <entities/HaEntitySwitch.h>
 #include <entities/HaEntityNumber.h>
 #include <entities/HaEntityText.h>
 #include <entities/HaEntityString.h>
 #include <entities/HaEntityTemperature.h>
 #include <entities/HaEntityHumidity.h>
#endif

#ifdef ESP32
#include <WiFi.h>
#elif ESP8266
#include <ESP8266WiFi.h>
#else
#error "Unsupported hardware. Sorry!"
#endif

#include "DHT.h"
#include <Adafruit_GFX.h>
#include <Adafruit_SSD1306.h>
#include <DFRobot_DHT20.h>
#include <SPI.h>
#include <Wire.h>


//DallasTemperature
#ifdef DS18B20xx

#include <DallasTemperature.h>
#define ONE_WIRE_BUS 7			//D4 - GPIO7, 
OneWire oneWire(ONE_WIRE_BUS);

// Pass oneWire reference to DallasTemperature library
DallasTemperature sensors(&oneWire);

DeviceAddress Thermometer;
int deviceCount = 0;
float sensor1val = 0;
float sensor2val = 0;
float sensor3val = 0; 
float tempC;

#endif

#define Button1 6                       // on/off
#define Button2 7                       // + increase
#define Button3 8                       // - decrease  
#define Heater 10
#define Fan 5

//#define Led 3

#ifdef DS18B20xx
 #define Led 3
#endif
#ifndef DS18B20xx
 #define Led 4
#endif

#define DHT_PIN 9 // The Arduino Nano pin connected to DHT21/22 sensor
#define DHT_TYPE DHT21
//#define DHT_TYPE DHT22 

#define SCREEN_WIDTH 128 
#define SCREEN_HEIGHT 64 

#define OLED_RESET 4  
#define SCREEN_ADDRESS 0x3C  
Adafruit_SSD1306 display(SCREEN_WIDTH, SCREEN_HEIGHT, &Wire, OLED_RESET);

DFRobot_DHT20 dht20;
DHT dht(DHT_PIN, DHT_TYPE);

bool FanRun = false;

bool HumOff = false;                       // AutoHum trigger 

unsigned long previousMillis = 0;
unsigned long AutoOffpreviousMillis = 0;
unsigned long AutoOffSetpreviousMillis = 0;
unsigned long FanOnpreviousMillis = 0;
unsigned long FanHumOnpreviousMillis = 0;
unsigned long debugMillis = 0;

#ifdef BlankScreen
#ifdef UsePixel
#ifdef BlankScreenAutoOff
unsigned long ScreenSaverpreviousMillis = 0;
#endif
#endif
#endif

int FanValue = 0;
bool FanValueSet = false;
int AutoOffTimeValue;
bool status = false;
bool Hot = false;
bool AutoOff = false;
bool AutoOffSet = false;
int AutoHumValue = 25; 
bool AutoHum = false;
bool AutoHumSet = false;
bool HeatMaxSet = false;
bool FanOn = false;
bool FanHumOn = false;
bool TempHigh = false;
bool showSecondTemp = false;
bool showLed = false;
bool showLedSet = false;
bool LedOn = false;
char text[] = "°C";
#ifdef debug
char textC[] = "°C";
char textF[] = "°F";
#endif 

float Temperature;
float TemperatureC;
float Humidity;
float Temperature2;
float Humidity2;
float tempDiff;
int TempSensor = 3;
int TempSensorMax = 0;
//int SensorCnt = 0;
float TempVal;
bool printAdr = false;
int device = 0;

int bild_h = 0;
int bild_w = 0; 
int bildpos = 0; 
bool screensaver = false;
bool screensaverOn = false;
bool screensaverSet = false;
int screensaverCnt = 0;
int screensaverCntX = 0;

char TempIntegerDisplay[4];
char TempFractionDisplay[4];
char HumIntegerDisplay[4];
char HumFractionDisplay[4];
char TargetTempDisplay[4];
char TargetHumDisplay[2];
char MinuteDisplay[4];

#ifdef HomeAssistant

 const char wifi_ssid[] = WIFI_SSID; 
 const char wifi_password[] = WIFI_PASS; 
 const char mqtt_client_id[] = MQTT_ID;
 const char mqtt_host[] = MQTT_HOST;
 const char mqtt_username[] = MQTT_USER;
 const char mqtt_password[] = MQTT_PASS;

IJsonDocument _json_this_device_doc;
void setupJsonForThisDevice() {
  _json_this_device_doc["identifiers"] = "my_hardware_" + std::string(mqtt_client_id);
  _json_this_device_doc["name"] = HAname;
  _json_this_device_doc["sw_version"] = swversion;
  _json_this_device_doc["model"] = "Arduino Nano ESP32-S3";
  _json_this_device_doc["manufacturer"] = "Werner Krenn";
}
MQTTRemote _mqtt_remote(mqtt_client_id, mqtt_host, 1883, mqtt_username, mqtt_password);

// Create the Home Assistant bridge. This is shared across all entities.
// We only have one per device/hardware. In our example, the name of our device is "drybox".
// See constructor of HaBridge for more documentation.
HaBridge ha_bridge(_mqtt_remote, HAnamelower, _json_this_device_doc);

HaEntityString _ha_entity_modetext(ha_bridge, HAmodetx, HAmodetxttxt);
HaEntityNumber _ha_entity_mode(ha_bridge, HAmode, HAmodetxt);	//1=off, 2=on, 3=autooff, 4=autohum

HaEntitySwitch _ha_entity_switch_heater(ha_bridge, HAsheater, HAsheatertxt);
HaEntitySwitch _ha_entity_switch_fan(ha_bridge, HAsfan, HAsfantxt);
#ifdef controlLed
 HaEntitySwitch _ha_entity_switch_led(ha_bridge, HAsled, HAsledtxt);
#endif

#ifndef Fahrenheit

HaEntityTemperature _ha_entity_temperature_target(ha_bridge, HAtemptarg, HAtemptargtxt);
HaEntityTemperature _ha_entity_temperature(ha_bridge, HAtemp, HAtemptxt);
HaEntityTemperature _ha_entity_temperature_2(ha_bridge, HAtemp2, HAtemp2txt);

#ifdef DS18B20HA
 #ifdef DallasSensor1
  HaEntityTemperature _ha_entity_temperature_e1(ha_bridge, HAsensor1, HAsensor1txt);
 #endif
 #ifdef DallasSensor2
  HaEntityTemperature _ha_entity_temperature_e2(ha_bridge, HAsensor2, HAsensor2txt);
 #endif
 #ifdef DallasSensor3
  HaEntityTemperature _ha_entity_temperature_e3(ha_bridge, HAsensor3, HAsensor3txt);
 #endif
#endif

#endif

#ifdef Fahrenheit
HaEntityTemperature _ha_entity_temperature_target(ha_bridge, HAtemptarg, HAtemptargtxt,
                                           HaEntityTemperature::Configuration{.unit = HaEntityTemperature::Unit::F,
                                                                              .force_update = false});
HaEntityTemperature _ha_entity_temperature(ha_bridge, HAtemp, HAtemptxt,
                                           HaEntityTemperature::Configuration{.unit = HaEntityTemperature::Unit::F,
                                                                              .force_update = false});
HaEntityTemperature _ha_entity_temperature_2(ha_bridge, HAtemp2, HAtemp2txt,
                                           HaEntityTemperature::Configuration{.unit = HaEntityTemperature::Unit::F,
                                                                              .force_update = false});

#ifdef DS18B20HA
 #ifdef DallasSensor1
  HaEntityTemperature _ha_entity_temperature_e1(ha_bridge, HAsensor1, HAsensor1txt,
                                           HaEntityTemperature::Configuration{.unit = HaEntityTemperature::Unit::F,
                                                                              .force_update = false});
 #endif
 #ifdef DallasSensor2
  HaEntityTemperature _ha_entity_temperature_e2(ha_bridge, HAsensor2, HAsensor2txt,
                                           HaEntityTemperature::Configuration{.unit = HaEntityTemperature::Unit::F,
                                                                              .force_update = false});
 #endif
 #ifdef DallasSensor3
  HaEntityTemperature _ha_entity_temperature_e3(ha_bridge, HAsensor3, HAsensor3txt,
                                           HaEntityTemperature::Configuration{.unit = HaEntityTemperature::Unit::F,
                                                                              .force_update = false});
 #endif
#endif

#endif

HaEntityHumidity _ha_entity_humidity_target(ha_bridge, HAhumtarg, HAhumtargtxt);
HaEntityHumidity _ha_entity_humidity(ha_bridge, HAhum, HAhumtxt);
HaEntityHumidity _ha_entity_humidity_2(ha_bridge, HAhum2, HAhum2txt);

#endif

bool _was_connected = false;
unsigned long _last_publish_ms = 0;
int iCount = 0; 


void setup(){
  Serial.begin(9600);
  //Serial.begin(115200);                             

  // Initialize buttons and heater
  pinMode(Button1, INPUT_PULLUP);
  pinMode(Button2, INPUT_PULLUP);
  pinMode(Button3, INPUT_PULLUP);
  pinMode(Heater, OUTPUT);
  pinMode(Fan, OUTPUT);
  pinMode(Led, OUTPUT);
  pinMode(LED_BLUE, OUTPUT);
  //pinMode(LED_BUILTIN, OUTPUT);

  #ifdef SecondTemp
    dht.begin(); // initialize the sensor
    showSecondTemp = true;
  #endif

  #ifdef controlLed
   showLed = true;
   digitalWrite(Led, HIGH);
   LedOn = true;
  #endif

  // Check if sensor and display are working
  if(dht20.begin()){
    Serial.println("Initialize sensor failed");
    delay(1000);
  }

 
  if(!display.begin(SSD1306_SWITCHCAPVCC, SCREEN_ADDRESS)) {
    Serial.println("Initialize display failed");
    delay(1000);
  }

  if (withDuct == true)
  {
   tempDiff = 0.1;
  } else {
   tempDiff = 0.2;
  }

  #ifndef Fahrenheit
   int HeatMaxValue= Max;
  #endif 

  #ifdef Fahrenheit
    TargetTemp = int((TargetTemp *9/5) + 32);
    MaxSet = int((MaxSet *9/5) + 32);
    int Max = int((Max *9/5) + 32);
    int HeatMax = int((HeatMax *9/5) + 32);
    int HeatMin = int((HeatMin *9/5) + 32);

    int HeatMaxValue= Max;
    MinSet = int((MinSet *9/5) + 32);
    char text[] = "°F"; 
 
   if (withDuct == true)
    {
     tempDiff = 0.18;
    } else {
     tempDiff = 0.36;
    } 
  #endif

  AutoHumValue = TargetHum;
  AutoOffTimeValue = AutoOffTime;
  FanValue = FanDelay;

  #ifdef HomeAssistant
   setupJsonForThisDevice(); // Populate json dict.

  // Setup WiFI
   WiFi.begin(wifi_ssid, wifi_password);
   while (WiFi.waitForConnectResult() != WL_CONNECTED) {
    Serial.println("Connection Failed! Rebooting...");
    delay(5000);
    ESP.restart();
   }
   Serial.println("have wifi");
   Serial.print("IP number: ");
   Serial.println(WiFi.localIP());

  #endif 

  #ifdef DS18B20xx

   #ifdef DallasSensor1
    TempSensorMax += 1; 
   #endif
   #ifdef DallasSensor2
    TempSensorMax += 1; 
   #endif
   #ifdef DallasSensor3
    TempSensorMax += 1; 
   #endif
   showSecondTemp = true;

   sensors.begin();
   //sensors.setResolution(TEMP_12_BIT); // Genauigkeit auf 12-Bit setzen
   /*
     9 Bit: 0,5 °C
    10 Bit: 0,25 °C
    11 Bit: 0,125 °C
    12 Bit: 0,0625 °C
   */
   delay(1000);
   sensors.requestTemperatures(); 

   Serial.println("Locating devices...");
   Serial.print("Found ");
   deviceCount = sensors.getDeviceCount();
   Serial.print(deviceCount, DEC);
   Serial.println(" devices.");
   Serial.println("");

  #endif

#ifdef WATCHDOG
  Serial.println("ESP started ...");            //Say hello to the world
  esp_task_wdt_deinit();
  esp_task_wdt_config_t wdt_config = {
    .timeout_ms = WDT_TIMEOUT * 1000,                 // Convertin ms
    .idle_core_mask = (1 << portNUM_PROCESSORS) - 1,  // Bitmask of all cores, https://github.com/espressif/esp-idf/blob/v5.2.2/examples/system/task_watchdog/main/task_watchdog_example_main.c
    .trigger_panic = true                             // ... ?Enable panic to restart ESP32
  };
  // WDT Init
  ESP32_ERROR = esp_task_wdt_init(&wdt_config);
   Serial.println("Last Reset : " + String(esp_err_to_name(ESP32_ERROR)));
   esp_task_wdt_add(NULL);  //add current thread to WDT watch

   //Serial.println(" Resetting WDT...");
   //esp_task_wdt_reset();
   // Serial.println("Disable watchdog");   //Write information to serial monitor
   // esp_task_wdt_deinit();                // Disable watchdog
#endif

  digitalWrite(LED_BLUE, HIGH);
  drawLogo();
  delay(2000); 
  sensorUpdate();
}

void loop(){
  // Heating system ON:
  while(status == true){
    unsigned long currentMillis = millis();
    FanOnpreviousMillis = currentMillis;

  if (AutoOff == true) {
     if(currentMillis - AutoOffpreviousMillis >= 60000) {     // AutoOff Time reached (check every 1 Minutes)
      AutoOffpreviousMillis = currentMillis;
      AutoOffTimeValue = AutoOffTimeValue - 1;
      if (AutoOffTimeValue <= 0){
      status = false;
      digitalWrite(Heater, LOW);
      if (FanValueSet == false) { FanSetting(); }
      }
     }
  }   

  if (AutoHum == true) {
     unsigned long currentMillisHum = millis();
     if (Humidity <= AutoHumValue - humDiff)
     { 
        digitalWrite(Heater, LOW); 
        if (FanValueSet == false) { FanSetting(); }
        HumOff = true;
        Hot = false;
        FanHumOn = true;
     }
     if ((Humidity >= AutoHumValue + humDiff))
     { 
        if (TempHigh == false)
        {
          if(Temperature < (TargetTemp - tempDiff))
          {
            digitalWrite(Fan, HIGH);
            FanRun = true;
            Hot = true;
          } 
        } 
        HumOff = false;
        FanHumOn = false;
     }

     if (HumOff == false) {FanHumOnpreviousMillis = currentMillisHum; }
     if (FanHumOn == true) {FanValue = FanDelay - ((currentMillisHum - FanHumOnpreviousMillis)/1000);}
     if (( FanHumOn == true) and ((currentMillisHum - FanHumOnpreviousMillis)/1000 >= FanDelay)) {     // Switch off Fan delay
        FanHumOn = false;
        digitalWrite(Fan, LOW);
        FanRun = false;
     }
     if ( (Hot == false) and (FanValue <=0)){
        digitalWrite(Fan, LOW);
        FanRun = false;
     }

  }

    if((digitalRead(Button2) == LOW) and (digitalRead(Button1) == LOW))
    {  
     AutoOffSet = true;
     AutoHum = false;
     AutoHumSet = false;
     AutoOffSetpreviousMillis = currentMillis;
     AutoOff = true;
    }

    if((digitalRead(Button3) == LOW) and (digitalRead(Button1) == LOW))
    {  
     AutoOffSet = false;
     AutoHum = true;
     AutoHumSet = true;
     AutoOffSetpreviousMillis = currentMillis;
     AutoOff = false;
     #ifdef BlankScreen 
     #ifdef UsePixel
     #ifdef BlankScreenAutoOff
      screensaver = true;
     #endif
     #endif 
     #endif

    }

    #ifdef SecondTemp 
    if((digitalRead(Button3) == LOW) and (digitalRead(Button2) == LOW))
    { 
     HeatMaxSet = true;  
     AutoOffSetpreviousMillis = currentMillis;
    }
    #endif

    if ((AutoOffSet == true) and (currentMillis - AutoOffSetpreviousMillis >= 30000) )       // after 30 seconds settings for AutoOffSet off
    {
     AutoOffSet = false;
    }

    if ((AutoHumSet == true) and (currentMillis - AutoOffSetpreviousMillis >= 30000) )       // after 30 seconds settings for AutoHumSet off
    {
     AutoHumSet = false;
    }

    #ifdef SecondTemp 
    if ((HeatMaxSet == true) and (currentMillis - AutoOffSetpreviousMillis >= 30000) )       // after 30 seconds settings for AutoHumSet off
    {
     HeatMaxSet = false;
    }
    
    #ifdef controlLed
    #ifdef ControllLedAutooff

    #ifdef Fahrenheit
    if ((showLed == true) and  (Temperature2 >= 140)) {
    showLedSet = true;
    digitalWrite(Led, LOW);
    LedOn = false;
    } 
    #endif
    #ifndef Fahrenheit
    if ((showLed == true) and  (Temperature2 >= 60)) {
    showLedSet = true;
    digitalWrite(Led, LOW);
    LedOn = false;
    } 
    #endif

    #endif 
    #endif
    
    #endif

    if ((digitalRead(Button1) == LOW) and (digitalRead(Button2) == HIGH) and (digitalRead(Button3) == HIGH) ){                 // Action button 1: switch heating system from on to off
      status = !status;
      AutoOff = false;
      AutoHum = false;
      AutoOffSet = false;
      AutoHumSet = false;
      AutoOffTimeValue = AutoOffTime;
      if (FanOn == true)
      {FanOnpreviousMillis = currentMillis;}
      sensorUpdate();
      digitalWrite(Heater, LOW);
      if (FanValueSet == false) { FanSetting(); }
      Hot = false;
      HeatMaxValue = Max;
      display.clearDisplay();
      drawStatus();
      if (status == true) {
       digitalWrite(Fan, HIGH);
       FanRun = true;
       FanOn = true;
      }
      if (not showSecondTemp){
       drawTemperature();
       drawHumidity();
      }
      else
      {
       drawTemperature1();
       drawHumidity1();
       drawTemperature2();
       drawHumidity2();
      }
      display.display(); 
      delay(200);
    }

    if(digitalRead(Button2) == LOW) {                 // Action button 2: increase target temperature
     if ((AutoOffSet == false) and (AutoHumSet == false) and (HeatMaxSet == false)) {
      TargetTemp = TargetTemp + 1;
      if (TargetTemp > MaxSet)
      { TargetTemp = MaxSet;}      
      previousMillis = currentMillis;
      display.clearDisplay();
      drawTargetTemperature();
     } 
     if ((AutoOffSet == true) and (AutoHumSet == false) and (HeatMaxSet == false))                          // or increase AutoOff time
     {                                          
      AutoOffTimeValue = AutoOffTimeValue + 10;
      if (AutoOffTimeValue > MaxAutoOffTime)
      { AutoOffTimeValue = MaxAutoOffTime; }
      previousMillis = currentMillis;
      display.clearDisplay();
      drawAutoOfftMinutes();
     }
     if ((AutoHumSet == true) and (AutoOffSet == false) and (HeatMaxSet == false))
     {
      AutoHumValue = AutoHumValue + 1;
      if (AutoHumValue > MaxHumSet)
      { AutoHumValue = MaxHumSet;}      
      previousMillis = currentMillis;
      display.clearDisplay();
      drawAutoHum();
     }
    #ifdef SecondTemp      
     if ((AutoHumSet == false) and (AutoOffSet == false) and (HeatMaxSet == true))
     {
      HeatMaxValue = HeatMaxValue + 1;
      if (HeatMaxValue > HeatMax)
      { HeatMaxValue = HeatMax;}      
      previousMillis = currentMillis;
      display.clearDisplay();
      drawHeatMax();
     }
    #endif

     display.display();
     delay(200);
    }

    if(digitalRead(Button3) == LOW) {                 // Action button 3: decrease target temperature

     #ifdef BlankScreen 
     #ifdef UsePixel
     #ifdef BlankScreenAutoOff
     if ((screensaverOn == true) and (AutoHum == true)) {
      screensaverCnt = 30;
      screensaverOn = false;
      screensaverSet = true;
      previousMillis = currentMillis;
      showData();
      }
     #endif
     #endif 
     #endif

    if ((AutoOffSet == false) and (AutoHumSet == false) and (HeatMaxSet == false) and (screensaverSet == false) ) {
      
       TargetTemp = TargetTemp - 1;
       if (TargetTemp < MinSet)
         { TargetTemp = MinSet;}
       previousMillis = currentMillis;
       display.clearDisplay();
       drawTargetTemperature();
     }

     if (AutoOffSet == true)
      {
       AutoOffTimeValue = AutoOffTimeValue - 10;
       if (AutoOffTimeValue <= 0 )
       { AutoOffTimeValue = 10; }
       previousMillis = currentMillis;
       display.clearDisplay();
       drawAutoOfftMinutes();
     }


     if ((AutoHumSet == true) and (AutoOffSet == false) and (HeatMaxSet == false) and (screensaverSet == false))
     {
       AutoHumValue = AutoHumValue - 1;
       if (AutoHumValue < MinHumSet)
       { AutoHumValue = MinHumSet;} 
       if (AutoHumValue < 23)
       {
        #ifdef Fahrenheit
         if (TargetTemp < 131) {
            TargetTemp = 131;
            FanDelay = 420; 
            FanValue = FanDelay;
         } 
        #endif
        #ifndef Fahrenheit
         if (TargetTemp < 55) {
            TargetTemp = 55;
            FanDelay = 420; 
            FanValue = FanDelay;
         } 
        #endif

       }
       previousMillis = currentMillis;
       display.clearDisplay();
       drawAutoHum();
     }


    #ifdef SecondTemp      
     if ((AutoHumSet == false) and (AutoOffSet == false) and (HeatMaxSet == true))
     {
      HeatMaxValue = HeatMaxValue - 1;
      if (HeatMaxValue < HeatMin)
      { HeatMaxValue = HeatMin;}      
      previousMillis = currentMillis;
      display.clearDisplay();
      drawHeatMax();
     }
    #endif

     display.display();
     delay(200);
    }

    if(currentMillis - previousMillis >= Refresh) {     // Refreshes data on the display (every x mseconds)
      previousMillis = currentMillis;
      sensorUpdate();
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

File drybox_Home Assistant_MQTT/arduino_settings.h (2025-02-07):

// Uncomment the next line if you want the temperature to be displayed in Fahrenheit, it is displayed in Celcius by default
// #define Fahrenheit

// to see the Temp/Hum Data and DS18B20 addresses in the Serial Monitor uncomment next line
#define debug

#define showFraction		// all values with decimal values otherwise only integer values
// If an LED strip needs to be controlled otherwise uncomment next line
#define controlLed
#define ControllLedAutooff	// Led on and Temperature >=60°C/140°F (= max. operating temperature LED strip) the led is switched off

// if have not attached a second temp/hum Sensor (dht22 or dht21) uncomment next line
#define SecondTemp		// should be placed on the floor under the heater or duct - not tested without this!
			// Showing of SecondTemp is now always on! Is needed for DS18B20 sensors
#define BlankScreen		// activate ScreenSaver with "down" Button - 
#define UsePixel		// ScreenSaver is "running Pixel" otherwise blank Screen
#define BlankScreenAutoOff            // if heating is off sreensaver active after 10 minutes - need also #UsePixel

#define WATCHDOG

//#define HomeAssistant		// send data to Homee Assistant

#ifdef HomeAssistant

 char HAname[12] = "Drybox2";
 char HAnamelower[12] = "drybox2";

 char HAmodetx[] = "Mode";
 char HAmode[] = "Mode";
 char HAsheater[] = "Switch Heater";
 char HAsfan[] = "Switch Fan";
 char HAsled[] = "Switch Led";

 char HAtemptarg[] = "Temperature Target";		//Sensor Name in Home Assistant
 char HAhumtarg[] = "Humidity Target";
 char HAtemp[] = "Temperature";
 char HAtemp2[] = "Temperature 2";
 char HAhum[] = "Humidity";
 char HAhum2[] = "Humidity 2";

 char HAmodetxttxt[] = "drybox_modetxt";
 char HAmodetxt[] = "drybox_mode";
 char HAsheatertxt[] = "drybox_switch_heater";
 char HAsfantxt[] = "drybox_switch_fan";
 char HAsledtxt[] = "drybox_switch_led";

 char HAtemptargtxt[] = "drybox_temperature_target";	//Entity-ID ( sensor.drybox_temperature_target )
 char HAhumtargtxt[] = "drybox_humidity_target";
 char HAtemptxt[] = "drybox_temperature";
 char HAtemp2txt[] = "drybox_temperature_2";
 char HAhumtxt[] = "drybox_humidity";
 char HAhum2txt[] = "drybox_humidity_2";

#define MQTT_ID "DryBox2"
#define WIFI_SSID "FRITZ!Box"		// your network SSID (name)
#define WIFI_PASS "????????????????????"	// your network password (use for WPA, or use as key for WEP)
#define MQTT_HOST "192.???.???.???"
#define MQTT_USER "Name"
#define MQTT_PASS "Password"

#endif

//#define DS18B20xx		// also support and show DS18B20 temperature sensors

#ifdef DS18B20xx
#define DS18B20HA         	//DS18B20 data also send to Home Assinstant

uint8_t sensor1[8] = { 0x28, 0x2C, 0xA8, 0x83, 0x00, 0x00, 0x00, 0x89 };
uint8_t sensor2[8] = { 0x28, 0x2B, 0x73, 0x85, 0x00, 0x00, 0x00, 0x2B };
uint8_t sensor3[8] = { 0x28, 0x57, 0x8A, 0x84, 0x00, 0x00, 0x00, 0x14 };

//#define DallasAdrSet		// are the DS18B20 temp sensors adresses above correct? Can be found with debug and seriell Monitor

#define DallasSensor1		// first DS18B20 temp sensors available
#define DallasSensor2		// second DS18B20 temp sensors available
#define DallasSensor3		// third DS18B20 temp sensors available

#ifdef HomeAssistant
 char HAsensor1[] = "Temperature e1";		//Sensor Name in Home Assistant
 char HAsensor2[] = "Temperature e2";
 char HAsensor3[] = "Temperature e3";

 char HAsensor1txt[] = "drybox_temperature_e1";		//Entity-ID ( sensor.drybox_temperature_e1 )
 char HAsensor2txt[] = "drybox_temperature_e2";
 char HAsensor3txt[] = "drybox_temperature_e3";
#endif

#endif

//#define PETG                         // Max = 73 °C	163
//#define ABS                          // Max = 83 °C	181
//#define ASA                          // Max = 93 °C	199
//#define PC                           // Max = 123 °C	253
//#define PA                           // Max = 143 °C	289

float TemperatureCor = 0.0;               // correction Temperatur
float HumidityCor = 0.0;                  // correction Humidity
float Temperature2Cor = 0.0;              // correction Temperatur2 if #define SecondTemp 
float Humidity2Cor = 0.0;                 // correction Humidity2 if #define SecondTemp

// all this Temperature values are need in °C
// If you select Fahrenheit, these values will later be converted for use in Fahrenheit
int Max = 85;                             // overHeating Temp under the duct, need #overHeat = true and SecondTemp
int HeatMaxValue = 85;
int HeatMax = 140;
int HeatMin = 70;
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

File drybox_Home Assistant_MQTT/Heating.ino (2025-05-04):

void sensorUpdate(){
  #ifdef DS18B20xx
   TempSensor = TempSensor + 1;
   if (TempSensor > TempSensorMax) {TempSensor = 0; }
  #endif
  
  #ifdef SecondTemp
    Temperature2 = dht.readTemperature() + Temperature2Cor;
    //Temperature_F = dht.readTemperature(true);
   #ifdef Fahrenheit
    Temperature2 = (Temperature2 *9/5) + 32;   // Converts temperature to fahrenheit if defined
    //Temperature2 = 103.3;
   #endif
    Humidity2 = dht.readHumidity() + Humidity2Cor;
   if (Humidity2 == Humidity2) {
     //Good value
    } else {
     Humidity2 = 0;
     Temperature2 = 0;
   }

  if (overHeat == true){
   if (Temperature2 >= HeatMaxValue)
      { TempHigh = true; }
   else
      { 
        TempHigh = false; 
      }
   } 
  #endif  

  Temperature = dht20.getTemperature() + TemperatureCor;        // Get temperature in degrees Celcius
  TemperatureC = Temperature;
  Humidity = (dht20.getHumidity()*100) + HumidityCor;        // Get relative humidity
  #ifdef Fahrenheit
    Temperature = (Temperature *9/5) + 32;   // Converts temperature to fahrenheit if defined
    //Temperature = 102.4;
  #endif
  if ((Humidity >= 115) or  (Humidity < 0)){
    Humidity = 0;
    Temperature = 0;
    TemperatureC = 50;
  }

#ifdef DS18B20xx
 sensors.requestTemperatures(); 

 #ifdef DallasSensor1
  #ifndef DallasAdrSet
   sensor1val = sensors.getTempCByIndex(0);
  #endif
  #ifdef DallasAdrSet
   sensor1val = sensors.getTempC(sensor1);
  #endif
  if ((sensor1val <= 0) or (sensor1val == 85.00) or (sensor1val >= 150.00))  {
    sensor1val  = 0;
  }
    #ifdef Fahrenheit
     if (sensor1val != 0){
     sensor1val = (sensor1val *9/5) + 32;  
     }
    #endif
 #endif
 #ifdef DallasSensor2
  #ifndef DallasAdrSet
   sensor2val = sensors.getTempCByIndex(1);
  #endif
  #ifdef DallasAdrSet
   sensor2val = sensors.getTempC(sensor2);
  #endif
  if ((sensor2val <= 0)  or (sensor2val == 85.00) or (sensor2val >= 150.00)){
    sensor2val  = 0;
  }  
    #ifdef Fahrenheit
     if (sensor2val != 0){
     sensor2val = (sensor2val *9/5) + 32;  
     }
    #endif
 #endif
 #ifdef DallasSensor3
  #ifndef DallasAdrSet
   sensor3val = sensors.getTempCByIndex(2);
  #endif
  #ifdef DallasAdrSet
   sensor3val = sensors.getTempC(sensor3);
  #endif
  if ((sensor3val <= 0) or (sensor3val == 85.00) or (sensor3val >= 150.00)){
    sensor3val  = 0;
  }  
    #ifdef Fahrenheit
     if (sensor3val != 0){
     sensor3val = (sensor3val *9/5) + 32;  
     }
    #endif
 #endif

#endif

}

void heater(){
  if (TempHigh == false)
  {
    if(Temperature < (TargetTemp - tempDiff))
    {
      if ((AutoHum == false) or ((AutoHum == true) and (HumOff == false)))
      digitalWrite(Heater, HIGH);            // Turns heating element on if more than 0.2 of 0.5 degrees celcius under the target temperature
      screensaverOn = false;
      if ((AutoHum == true) and (FanHumOn == true))
      { 
      digitalWrite(Fan, HIGH);
      }
      else { digitalWrite(Fan, HIGH); }
      FanRun = true;
      Hot = true;
      if (FanValue > 0 ) {screensaverCnt = 0; }
    } 
    if ((Temperature > (TargetTemp + tempDiff)) or ((AutoHum == true) and (HumOff == true ))){      // Turns heating element off if more than 0.2 or 0.5 degrees celcius over the target temperature
      digitalWrite(Heater, LOW);
      //if ((FanValueSet == false) and (FanValue>0) ) { FanSetting(); }
      Hot = false;  
      if ((AutoHum == true) and (FanValue <=0)) {
       if (screensaver == true) {
        if ((screensaverSet == true) and (screensaverCnt <=29)) {screensaverSet = false;}
        if (screensaverCnt <= 0) { screensaverOn = true; }
        if (screensaverOn == false) {screensaverCnt -= 1; }
        } 
       digitalWrite(Fan, LOW);
       FanRun = false; 
      }   
    } 
    if (Hot == true) {FanValueSet = false;}
  }
  else { digitalWrite(Heater, LOW); }
}

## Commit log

2024-10-23 Update README.md
    Added Comparison with/without duct, with/without additional fans
2024-10-30 Photos show connection Sensor2
2025-01-06 MQTT support for Home Assistant
    Arduino IDE files for Arduino Nano ESP32-S3
2025-01-16 Now with support for DS18B20 temp sensor
    All configurations and settings now in arduino_settings.h. In zip-file is arduino_settings_.h.
    This will not overwrite an existing settings file.
    If arduino_settings.h. does not exist, rename arduino_settings_.h to arduino_settings.h. and make your own settings there.
2025-01-29 Add files via upload
    Now with screensaver. The names for Home Assistant can you now set in arduino_settings.h too.
2025-05-04 Temperatures above 150°C !
    Temperatures above 150°C are now also ignored happend with DS18B20
2025-08-15 Update Drybox2.ino
    LED on and off moved to dedicated methods so they can be called from other code
2025-08-15 Update Mqtt.ino
    Listen for LED state changes coming from Home Assistant
2025-08-15 ledon, ledoff
